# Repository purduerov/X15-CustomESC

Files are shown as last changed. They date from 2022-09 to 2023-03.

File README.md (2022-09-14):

# Readme for X15-CustomESC

Whenever you make a new part, download the datasheet and save it here _**and**_ with the part in the parts library

Always pull other people's changes before beginning to work
`git pull`

Be sure to push your changes after  working on them. Run:
1. `git add .` to add any files in this directory or a subdirectory
or `git add -u` to add any modified files
2. (Optional) `git clean -nX` to see what ignored files can be removed
	`git clean -fX` removes ignored files (Eagle backups)
3. `git commit -m "helpful commit message"` with a description of the work that you did
4. `git push` to push your work to github

Other helpful commands
* `git status` says information about modified and staged files
* `git log` shows the recent commits of the repository
* `git log filename.extension` show the recent commits for just that file
* `git checkout first-couple-letter-of-commit-id` lets you go back to a previous version
* `git checkout master` brings you back to the latest commit
* `git tag` lists the tags
* `git tag -a orderX -m "the version of the board placed for the X'th order"` tag a specific commit
* `git push --tags` needed to push tags to remote
* `git show orderX` show the commit log for the given tag
* `git checkout orderX` go back and interact with the files at the tagged commit

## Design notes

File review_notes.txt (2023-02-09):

Put the reset button closer to the STM32
Put the supply indicator LEDs closer to the actual supply, and the test LEDs near the test points they're connected to
Something seems wrong with the diodes on the MOSFET switching circuits. The part is not working properly on the board.
Make ground lines thicker, and make the supply lines to the output much bigger

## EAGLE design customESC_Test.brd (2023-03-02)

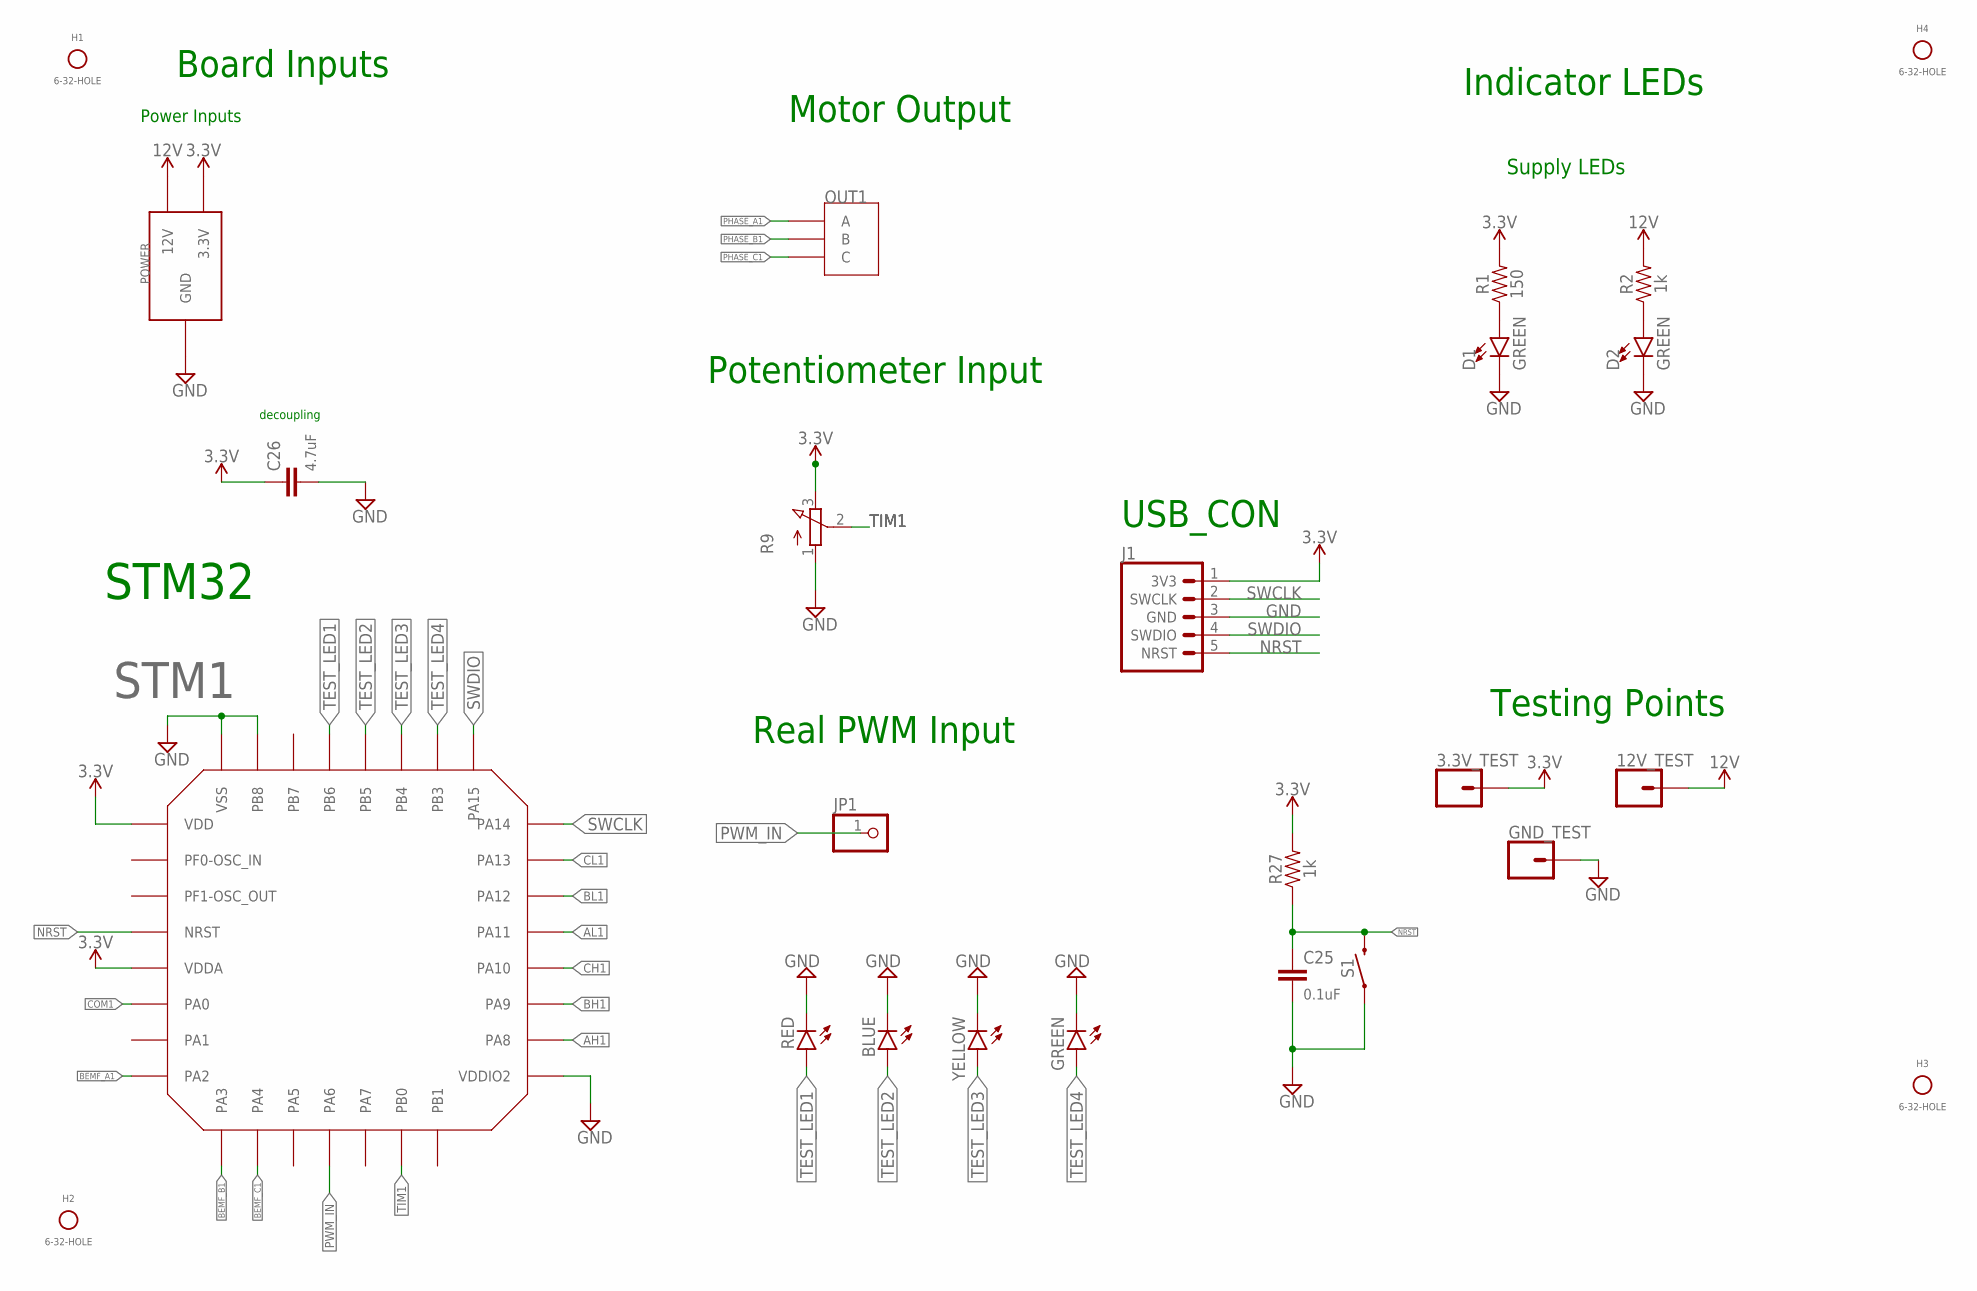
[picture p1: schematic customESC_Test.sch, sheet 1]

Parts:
3.3V_TEST, 12V_TEST: CONN_01; 1X01
BLUE: LEDCHIPLED_0805; CHIPLED_0805
C25: 0.1uF; 0603
C26: 4.7uF; 0603
D1, D2: GREEN; LED-0603
GND_TEST: CONN_01; 1X01
GREEN: LEDCHIPLED_0805; CHIPLED_0805
H1, H2, H3, H4: 6-32-HOLE; MOUNTING_HOLE
J1: 3V3 -SWCLK-GND-SWDIO- NRST; 1X05
JP1: PINHD-1X1; 1X01
OUT1: IPBT-103-H1-T-S
POWER: 12V-CONNECTOR
R1: 150; 0603
R2, R27: 1k; 0603
R9: 3RP/1610N
RED: LEDCHIPLED_0805; CHIPLED_0805
S1: MOMENTARY-SWITCH-SPST-SMD-6.0X3.5MM; TACTILE_SWITCH_SMD_6.0X3.5MM
STM1: STM32F042K6T6
YELLOW: LEDCHIPLED_0805; CHIPLED_0805

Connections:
AH1: STM1.PA8; also elsewhere on the board
AL1: STM1.PA11; also elsewhere on the board
BEMF_A1: STM1.PA2; also elsewhere on the board
BEMF_B1: STM1.PA3; also elsewhere on the board
BEMF_C1: STM1.PA4; also elsewhere on the board
BH1: STM1.PA9; also elsewhere on the board
BL1: STM1.PA12; also elsewhere on the board
CH1: STM1.PA10; also elsewhere on the board
CL1: STM1.PA13; also elsewhere on the board
COM1: STM1.PA0; also elsewhere on the board
GND: BLUE.C, C25.2, C26.2, D1.C, D2.C, GND_TEST.1, GREEN.C, J1.3 (GND), POWER.GND, POWER.GND@1 (GND), POWER.GND@2 (GND), POWER.GND@3 (GND), POWER.GND@4 (GND), POWER.GND@5 (GND), POWER.GND@6 (GND), POWER.GND@7 (GND), POWER.GND@8 (GND), POWER.GND@9 (GND), POWER.GND@10 (GND), POWER.GND@11 (GND), POWER.GND@12 (GND), R9.1 (A), RED.C, S1.1, STM1.PB8-BOOT0 (PB8), STM1.VDDIO2, STM1.VSS, STM1.VSS1 (VSS), YELLOW.C; also elsewhere on the board
unnamed: D1.A, R1.1
unnamed: D2.A, R2.1
NRST: C25.1, J1.5 (NRST), R27.1, S1.2, STM1.NRST
PHASE_A1: OUT1.1 (A); also elsewhere on the board
PHASE_B1: OUT1.2 (B); also elsewhere on the board
PHASE_C1: OUT1.3 (C); also elsewhere on the board
PWM_IN: JP1.1, STM1.PA6
SWCLK: J1.2 (SWCLK), STM1.PA14
SWDIO: J1.4 (SWDIO), STM1.PA15
TEST_LED1: RED.A, STM1.PB6
TEST_LED2: BLUE.A, STM1.PB5
TEST_LED3: STM1.PB4, YELLOW.A
TEST_LED4: GREEN.A, STM1.PB3
TIM1: R9.2 (S), STM1.PB0
VCC_1: 3.3V_TEST.1, C26.1, J1.1 (3V3), POWER.3.3V, R1.2, R9.3 (E), R27.2, STM1.VDD, STM1.VDDA
VCC_2: 12V_TEST.1, POWER.12V@1 (12V), POWER.12V@2 (12V), POWER.12V@3 (12V), POWER.12V@4 (12V), POWER.12V@5 (12V), POWER.12V@6 (12V), POWER.12V@7 (12V), POWER.12V@8 (12V), POWER.12V@9 (12V), POWER.12V@10 (12V), POWER.12V@11 (12V), POWER.12V@12 (12V), R2.2; also elsewhere on the board

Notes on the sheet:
Supply LEDs
Power Inputs
Motor Output
STM32
decoupling
Indicator LEDs
Testing Points
Board Inputs
Potentiometer Input
Real PWM Input
USB_CON

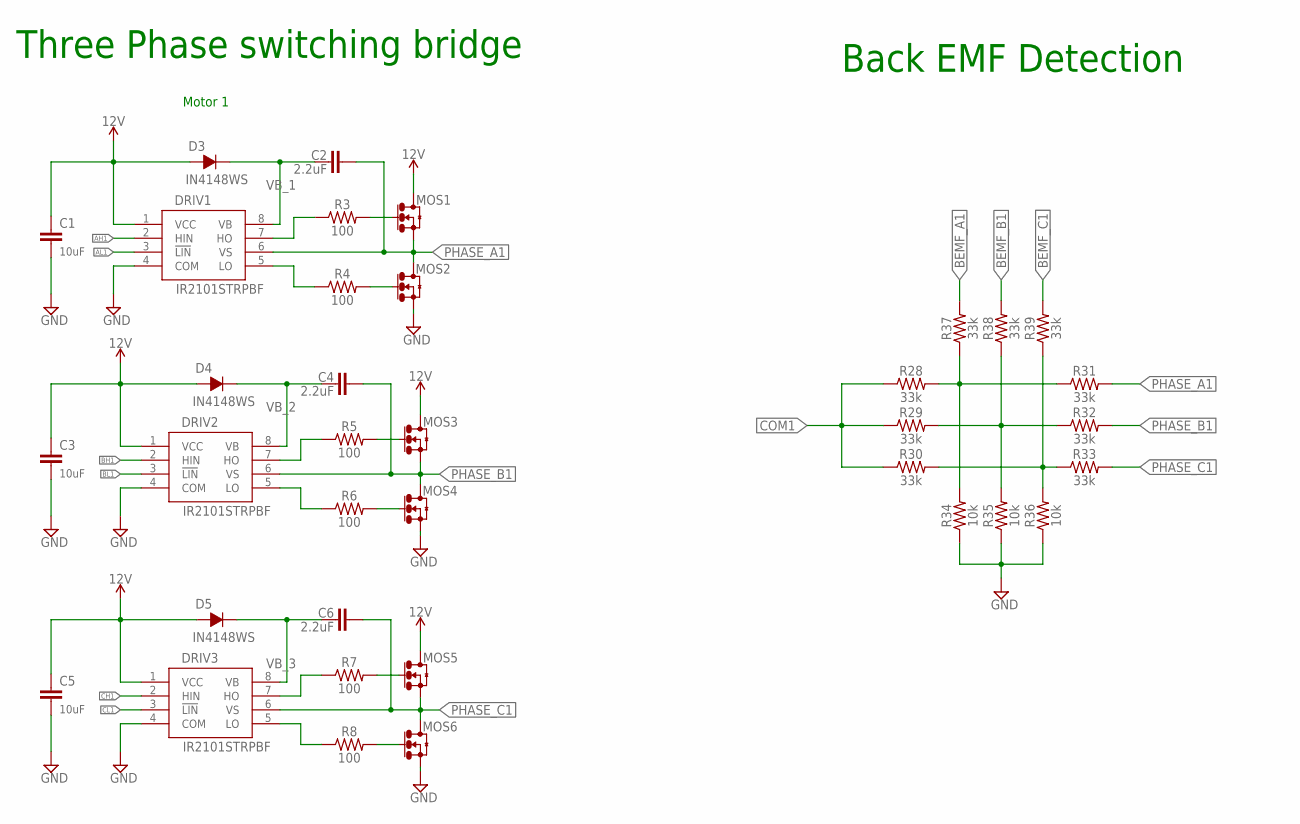
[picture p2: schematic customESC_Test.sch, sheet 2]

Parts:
C1, C3, C5: 10uF; 0603
C2, C4, C6: 2.2uF; 0603
D3, D4, D5: IN4148WS
DRIV1, DRIV2, DRIV3: IR2101STRPBF
MOS1, MOS2, MOS3, MOS4, MOS5, MOS6: IRLR7843TRPBF
R3, R4, R5, R6, R7, R8: 100; 0603
R28, R29, R30, R31, R32, R33, R37, R38, R39: 33k; 0603
R34, R35, R36: 10k; 0603

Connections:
AH1: DRIV1.2 (HIN); also elsewhere on the board
AL1: DRIV1.3 (!LIN); also elsewhere on the board
BEMF_A1: R37.2; also elsewhere on the board
BEMF_B1: R38.2; also elsewhere on the board
BEMF_C1: R39.2; also elsewhere on the board
BH1: DRIV2.2 (HIN); also elsewhere on the board
BL1: DRIV2.3 (!LIN); also elsewhere on the board
CH1: DRIV3.2 (HIN); also elsewhere on the board
CL1: DRIV3.3 (!LIN); also elsewhere on the board
COM1: R28.1, R29.1, R30.1; also elsewhere on the board
GND: C1.2, C3.2, C5.2, DRIV1.4 (COM), DRIV2.4 (COM), DRIV3.4 (COM), MOS2.2 (DRAIN), MOS2.4 (DRAIN), MOS4.2 (DRAIN), MOS4.4 (DRAIN), MOS6.2 (DRAIN), MOS6.4 (DRAIN), R34.1, R35.1, R36.1; also elsewhere on the board
unnamed: DRIV1.7 (HO), R3.1
unnamed: MOS1.1 (GATE), R3.2
unnamed: DRIV1.5 (LO), R4.1
unnamed: MOS2.1 (GATE), R4.2
unnamed: DRIV2.7 (HO), R5.1
unnamed: DRIV2.5 (LO), R6.1
unnamed: MOS3.1 (GATE), R5.2
unnamed: MOS4.1 (GATE), R6.2
unnamed: DRIV3.7 (HO), R7.1
unnamed: DRIV3.5 (LO), R8.1
unnamed: MOS5.1 (GATE), R7.2
unnamed: MOS6.1 (GATE), R8.2
unnamed: R28.2, R31.1, R34.2, R37.1
unnamed: R29.2, R32.1, R35.2, R38.1
unnamed: R30.2, R33.1, R36.2, R39.1
PHASE_A1: C2.2, DRIV1.6 (VS), MOS1.2 (DRAIN), MOS1.4 (DRAIN), MOS2.3 (SOURCE), R31.2; also elsewhere on the board
PHASE_B1: C4.2, DRIV2.6 (VS), MOS3.2 (DRAIN), MOS3.4 (DRAIN), MOS4.3 (SOURCE), R32.2; also elsewhere on the board
PHASE_C1: C6.2, DRIV3.6 (VS), MOS5.2 (DRAIN), MOS5.4 (DRAIN), MOS6.3 (SOURCE), R33.2; also elsewhere on the board
VB_1: C2.1, D3.P$2, DRIV1.8 (VB)
VB_2: C4.1, D4.P$2, DRIV2.8 (VB)
VB_3: C6.1, D5.P$2, DRIV3.8 (VB)
VCC_2: C1.1, C3.1, C5.1, D3.P$1, D4.P$1, D5.P$1, DRIV1.1 (VCC), DRIV2.1 (VCC), DRIV3.1 (VCC), MOS1.3 (SOURCE), MOS3.3 (SOURCE), MOS5.3 (SOURCE); also elsewhere on the board

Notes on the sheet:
Three Phase switching bridge
Motor 1
Back EMF Detection

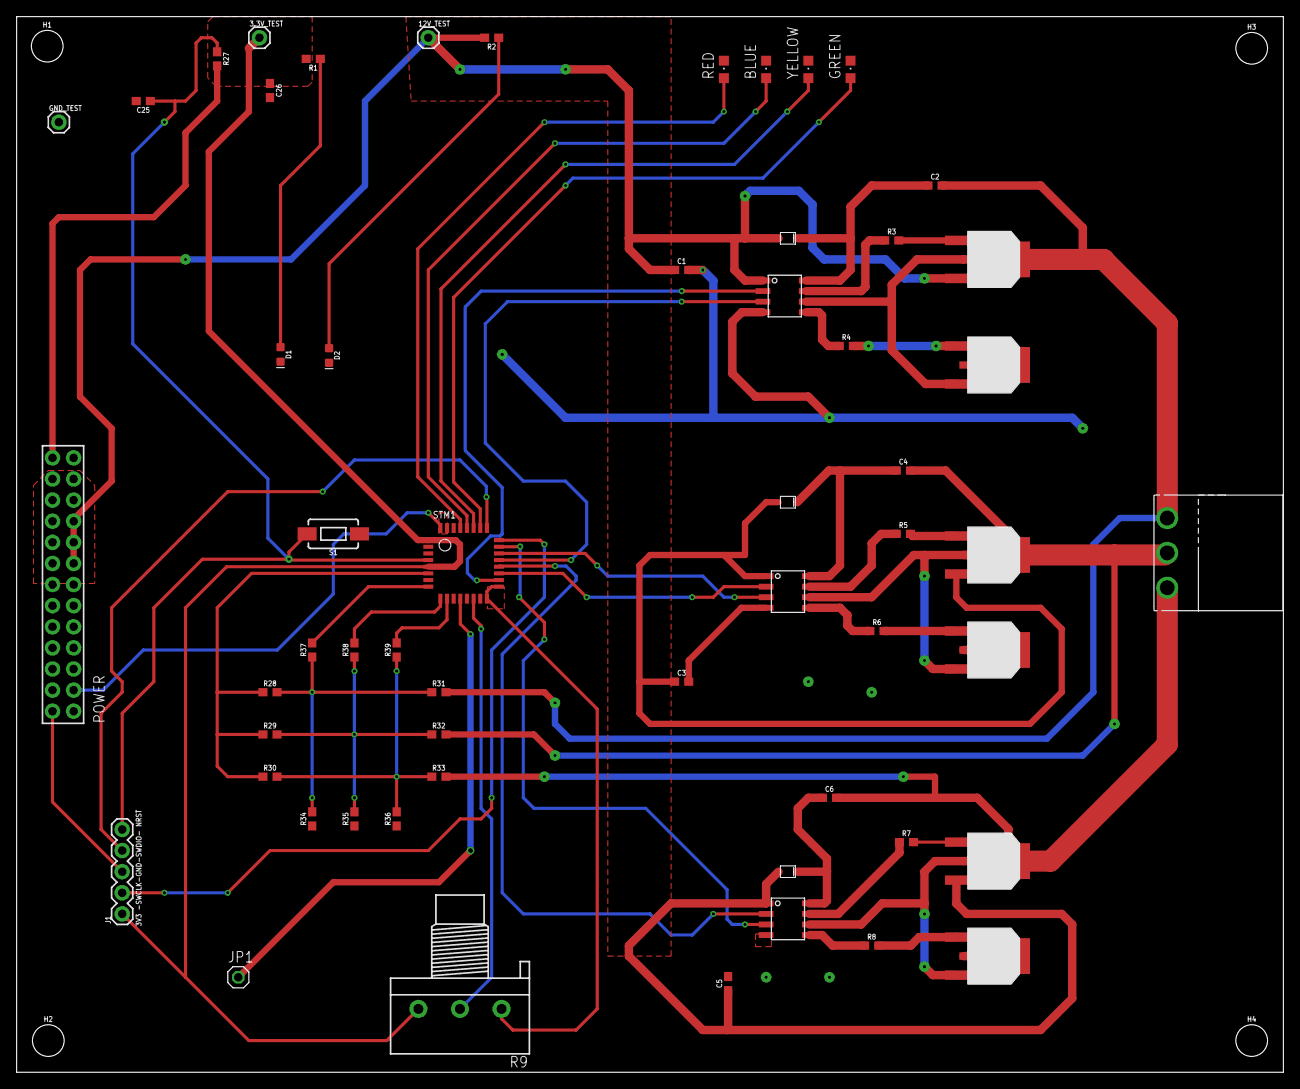
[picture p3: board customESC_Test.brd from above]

Board: 2 copper layers, 152.4 x 127.0 mm, 61 parts (0 on the bottom side), 45 nets.

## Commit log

2022-10-22 Started the schematic
    [customESC.sch]
2022-11-10 Made some progress on schematic
    [customESC.sch]
2022-11-12 Ready for design review? not really
    [customESC.sch]
2022-11-12 Finished main schematic
    [customESC.sch]
2022-11-17 Added a new file
    [customESC_Test_Board.sch]
2022-11-17 change name
    [customESC_Test.sch]
2022-11-17 name change
    [customESC.sch]
2022-12-01 update
    lol
    [customESC_Test.brd, customESC_Test.sch]
2022-12-03 IM DOING WORK AT 4AM
    I LOVE ROV!!!!!!!!!!!!!!!!!!!!!!!!!!!!!!!!!!!!!!!!!!!!
    [customESC_Test.brd]
2022-12-03 Catherine Check off
    Hello
    [customESC_Test.brd]
2022-12-04 Finished first draft
    Need a design review before ordering
    [customESC_Test.brd]
2022-12-08 Fixed issues from design review
    [customESC_Test.brd]
2023-01-21 added paths for input and added test leds. needs a design review
    [customESC_Test.brd]
2023-01-26 last one
    [customESC_Test.brd]
2023-02-09 Yusuf, check review_notes.txt
    [customESC.sch]
2023-02-11 updates on supply line and moved the leds and reset button
    [customESC_Test.brd]
2023-03-02 Fixed it Raghav
    Hi
    [customESC_Test.brd, customESC_Test.sch]

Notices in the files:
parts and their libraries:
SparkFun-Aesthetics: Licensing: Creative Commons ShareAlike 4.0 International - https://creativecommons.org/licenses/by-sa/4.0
